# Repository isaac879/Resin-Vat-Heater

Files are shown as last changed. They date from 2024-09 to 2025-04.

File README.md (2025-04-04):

# Resin-Vat-Heater
This project is a vat heater for resin 3D printers. It is designed to keep the resin warm at an optimal temperature to ensure consistent and high quality prints.

The code is developed for a custom control board based on an ESP32-C3 and an E-Ink (E-Paper, GDEH0154D67) display module.

Important:
The E-Ink display lines “RES” and “CS” are mislabelled on the control board and to have the wires swapped. This has already been implemented in the code (See: resin_vat_heater_control_board.ino Line 33/Pin declarations). This prevents the “RES” line from pulling GPIO2 low causing issues uploading the code.

Make sure the element resistance is correct in the code and matches the resistance of your heating elements (Line 90: ELEMENT_RESISTANCE). 

Project video: https://youtu.be/hyjGFaW69lo

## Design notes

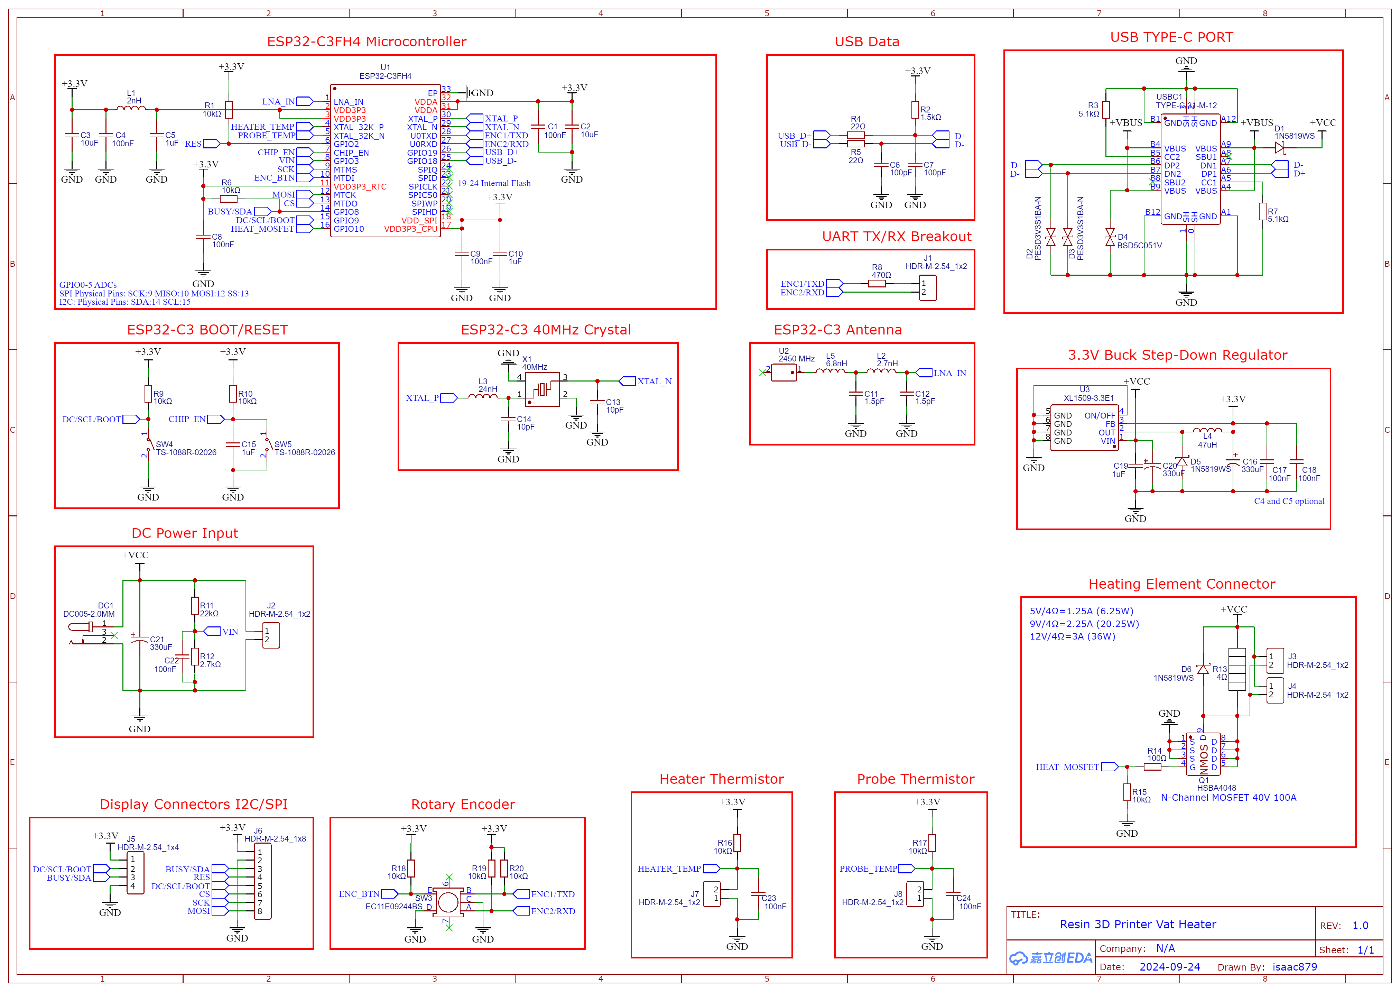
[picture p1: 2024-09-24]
Schematic-PCB/Control Board/Schematic_Resin-Vat-Hater_2024-09-24.png

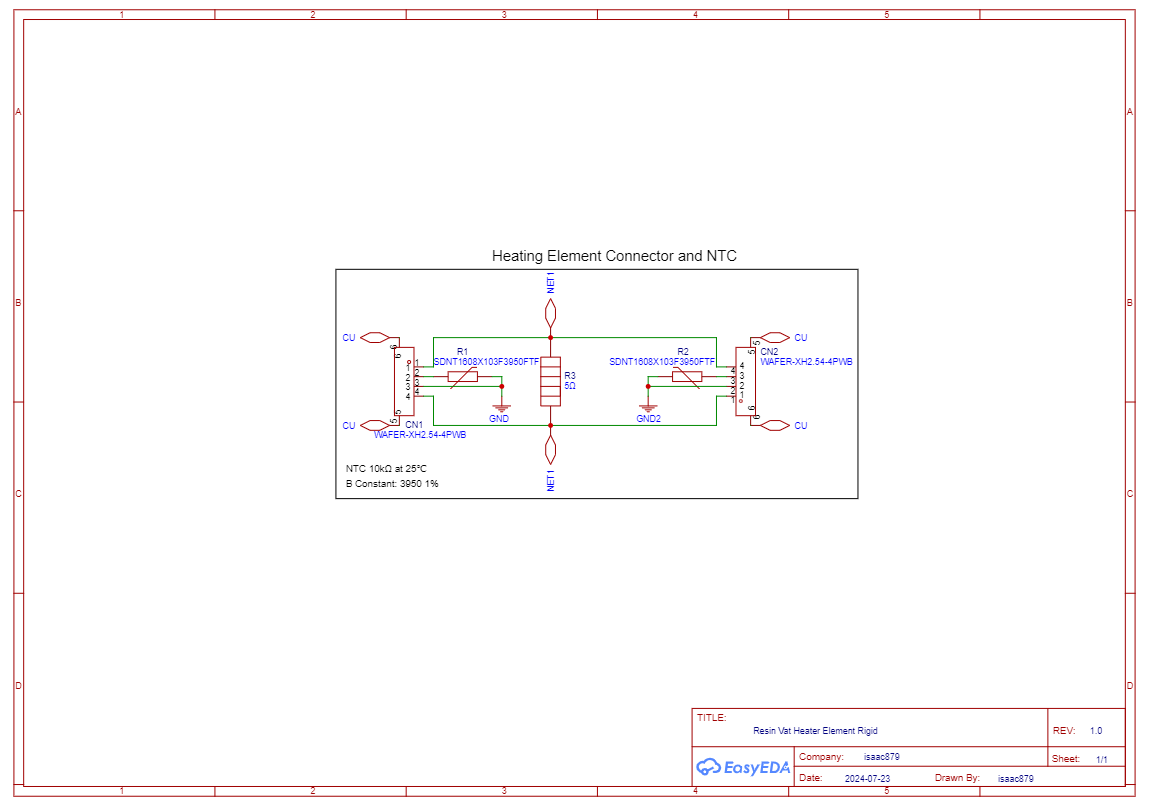
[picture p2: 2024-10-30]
Schematic-PCB/Heating Element/SCH_Resin Vat Heater Element_1-Resin Vat Heater Element_2024-10-30.png

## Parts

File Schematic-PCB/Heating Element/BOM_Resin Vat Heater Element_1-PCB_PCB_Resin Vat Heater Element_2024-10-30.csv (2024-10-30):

No. | Quantity | Comment | Designator | Footprint | Value | Manufacturer Part | Manufacturer | Supplier Part | Supplier
1 | 2 | WAFER-XH2.54-4PWB | CN1,CN2 | CONN-TH_4P-P0.20_XUNPU_WAFER-XH2.54-4PWB |  | WAFER-XH2.54-4PWB | XUNPU(讯普) | C3029478 | LCSC
2 | 2 | SDNT1608X103F3950FTF | R1,R2 | R0603 |  | SDNT1608X103F3950FTF | Sunlord(顺络) | C279936 | LCSC

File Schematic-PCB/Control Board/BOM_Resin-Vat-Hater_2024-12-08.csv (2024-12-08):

ID | Name | Designator | Footprint | Quantity | Manufacturer Part | Manufacturer | Supplier | Supplier Part | Price
1 | TYPE-C-31-M-12 | USBC1 | USB-C_SMD-TYPE-C-31-M-12MOD | 1 | TYPE-C-31-M-12 | Rectangular Connectors - Contacts | LCSC | C165948 | 0.155
2 | 1uF | C19 | C0805MOD | 1 | CL21B105KBFNNNE | SAMSUNG(三星) | LCSC | C28323 | 0.008
3 | 100nF | C1,C4,C17,C18 | C0603 | 4 | CC0603KRX7R9BB104 | YAGEO | LCSC | C14663 | 0.002
4 | 330uF | C20,C21 | CAP-SMD_BD10.0-L10.3-W10.3-LS11.3-FD | 2 | RVE1V331M1010 | HONOR(荣誉) | LCSC | C88682 | 0.114
5 | 40MHz | X1 | CRYSTAL-SMD_4P-L3.2-W2.5-BL_SIT8008BI | 1 | CF4040M00015001 | HUAXIN(华昕) | LCSC | C7294600 | 0.052
6 | 6.8nH | L5 | L0603 | 1 | SDCL1608C6N8JTDF | Sunlord(顺络) | LCSC | C49447 | 0.008
7 | 10kΩ | R1,R6,R9,R10,R15,R16,R17 | R0603 | 7 | 0603WAF1002T5E | UNI-ROYAL(厚声) | LCSC | C25804 | 0.001
8 | TS-1088R-02026 | SW4,SW5 | SW-SMD_L3.9-W3.0-P4.45 | 2 | TS-1088R-02026 | XUNPU(讯普) | LCSC | C455280 | 0.044
9 | 10uF | C2,C3 | C0603 | 2 | CL10A106KP8NNNC | SAMSUNG(三星) | LCSC | C19702 | 0.005
10 | 1uF | C5,C10,C15 | C0603 | 3 | CL10A105KB8NNNC | SAMSUNG(三星) | LCSC | C15849 | 0.004
11 | 100nF | C8,C9,C22,C23,C24 | C0603 | 5 | CC0603KRX7R9BB104 | YAGEO(国巨) | LCSC | C14663 | 0.002
12 | 1.5pF | C11,C12 | C0603 | 2 | 0603CG1R5C500NT | FH(风华) | LCSC | C1639 | 0.003
13 | 10pF | C13,C14 | C0603 | 2 | CL10C100JB8NNNC | SAMSUNG(三星) | LCSC | C1634 | 0.003
14 | 330uF | C16 | CAP-SMD_BD6.3-L6.6-W6.6-FD | 1 | RVT1A331M0607 | HONOR | LCSC | C58277 | 0.034
15 | 1N5819WS | D1,D5,D6 | SOD-323_L1.8-W1.3-LS2.5-RD | 3 | 1N5819WS | Hottech(合科泰) | LCSC | C191023 | 0.008
16 | PESD3V3S1BA-N | D2,D3 | SOD-523_L1.2-W0.8-LS1.6-BI | 2 | PESD3V3S1BA-N | Bourne Semicon (Shenzhen) | LCSC | C316037 | 0.03
17 | BSD5C051V | D4 | SOD-523_L1.2-W0.8-LS1.6-BI | 1 | BSD5C051V | BORN | LCSC | C151981 | 0.026
18 | DC005-2.0MM | DC1 | DC-IN-TH_DC005 | 1 | DC005-2.0MM | SOFNG | LCSC | C111567 | 0.138
19 | 2nH | L1 | L0603 | 1 | SDCL1608C2N0STDF | Sunlord(顺络) | LCSC | C370234 | 0.008
20 | 2.7nH | L2 | L0603 | 1 | SDCL1608C2N7STDF | Sunlord(顺络) | LCSC | C13817 | 0.008
21 | 24nH | L3 | L0603 | 1 | SDCL1608C24NJTDF | Sunlord(顺络) | LCSC | C74305 | 0.007
22 | 47uH | L4 | IND-SMD_L5.0-W5.0 | 1 | CKCS5020-47uH/M | CENKER | LCSC | C354600 | 0.061
23 | HSBA4048 | Q1 | POWERPAK-SO-8_L6.2-W5.2-P1.27-BL-EP | 1 | HSBA4048 | HUASHUO(华朔) | LCSC | C508827 | 0.63
24 | 1.5kΩ | R2 | R0603 | 1 | 0603WAF1501T5E | UNI-ROYAL(厚声) | LCSC | C22843 | 0.001
25 | 22Ω | R4,R5 | R0603 | 2 | 0603WAF220JT5E | UNI-ROYAL(厚声) | LCSC | C23345 | 0.001
26 | 470Ω | R8 | R0603 | 1 | 0603WAF4700T5E | UNI-ROYAL(厚声) | LCSC | C23179 | 0.001
27 | 22kΩ | R11 | R0603 | 1 | 0603WAF2202T5E | UNI-ROYAL(厚声) | LCSC | C31850 | 0.001
28 | 2.7kΩ | R12 | R0603 | 1 | 0603WAF2701T5E | UNI-ROYAL(厚声) | LCSC | C13167 | 0.001
29 | 100Ω | R14 | R0603 | 1 | 0603WAF1000T5E | UNI-ROYAL(厚声) | LCSC | C22775 | 0.001
30 | EC11E09244BS | SW3 | SW-TH_EC11XXXXXXXX | 1 | EC11E09244BS | ALPSALPINE(阿尔卑斯阿尔派) | LCSC | C470742 | 1.661
31 | ESP32-C3FH4 | U1 | QFN-32_L5.0-W5.0-P0.50-TL-EP3.7 | 1 | ESP32-C3FH4 | ESPRESSIF(乐鑫) | LCSC | C2858491 | 2.308
32 | 2450 MHz | U2 | FILTER-SMD_1206-2P-L3.2-W1.6-L | 1 | RFANT3216120A5T | Walsin(华新科) | LCSC | C127629 | 0.079
33 | XL1509-3.3E1 | U3 | SOP-8_L4.9-W3.9-P1.27-LS6.0-BL | 1 | XL1509-3.3E1 | XLSEMI | LCSC | C74193 | 0.24
34 | 5.1kΩ | R3,R7 | R0603 | 2 | 0603WAF5101T5E | UNI-ROYAL(厚声) | LCSC | C23186 | 0.001

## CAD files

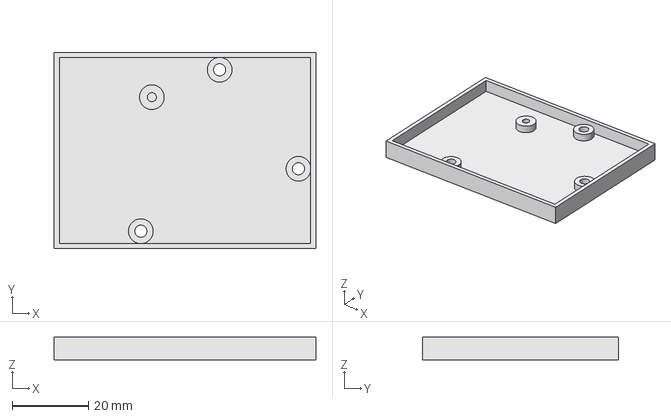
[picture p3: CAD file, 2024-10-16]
CAD FIles/STEP/PCB Case Bottom.step
68.8 x 51.6 x 6.00 mm

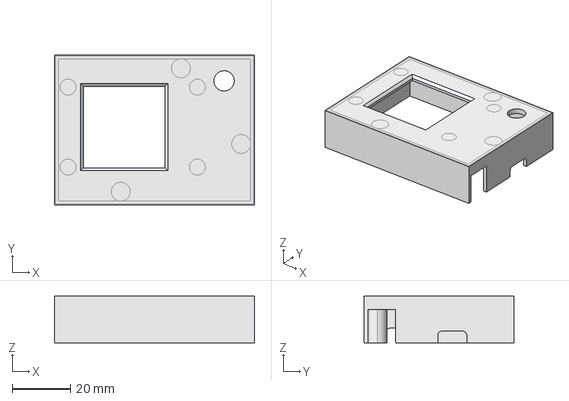
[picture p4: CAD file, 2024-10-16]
CAD FIles/STEP/PCB Case Top.step
68.8 x 51.6 x 16.0 mm

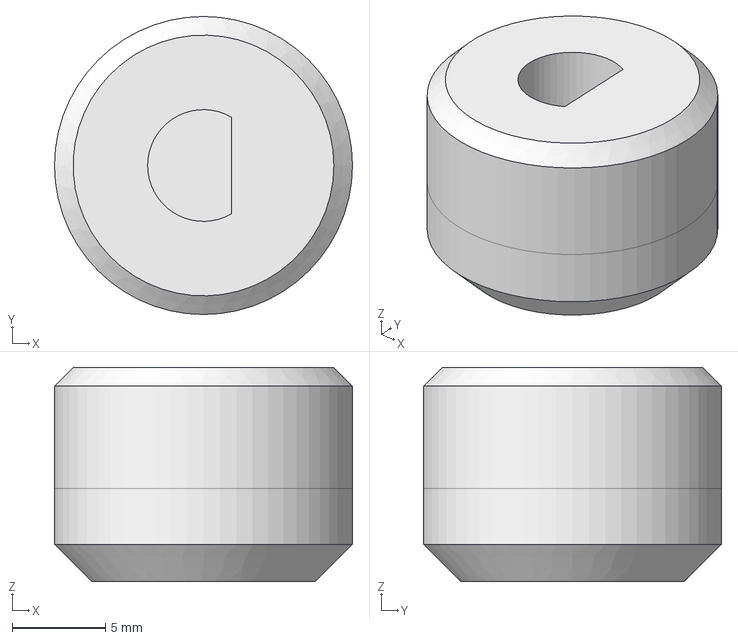
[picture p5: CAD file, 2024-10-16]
CAD FIles/STEP/Encoder knob.step
16.0 x 16.0 x 11.5 mm

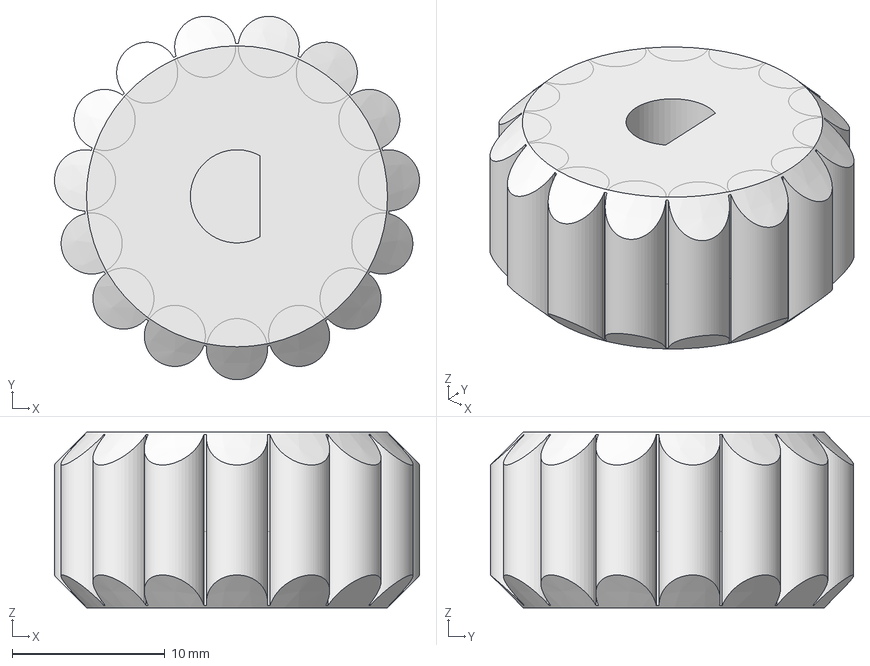
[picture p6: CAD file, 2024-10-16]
CAD FIles/STEP/Encoder knob 2.step
23.9 x 23.8 x 11.5 mm

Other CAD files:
CAD FIles/STLs/Encoder knob 2.stl
CAD FIles/STLs/Encoder knob.stl
CAD FIles/STLs/PCB Case Bottom.stl
CAD FIles/STLs/PCB Case Top.stl

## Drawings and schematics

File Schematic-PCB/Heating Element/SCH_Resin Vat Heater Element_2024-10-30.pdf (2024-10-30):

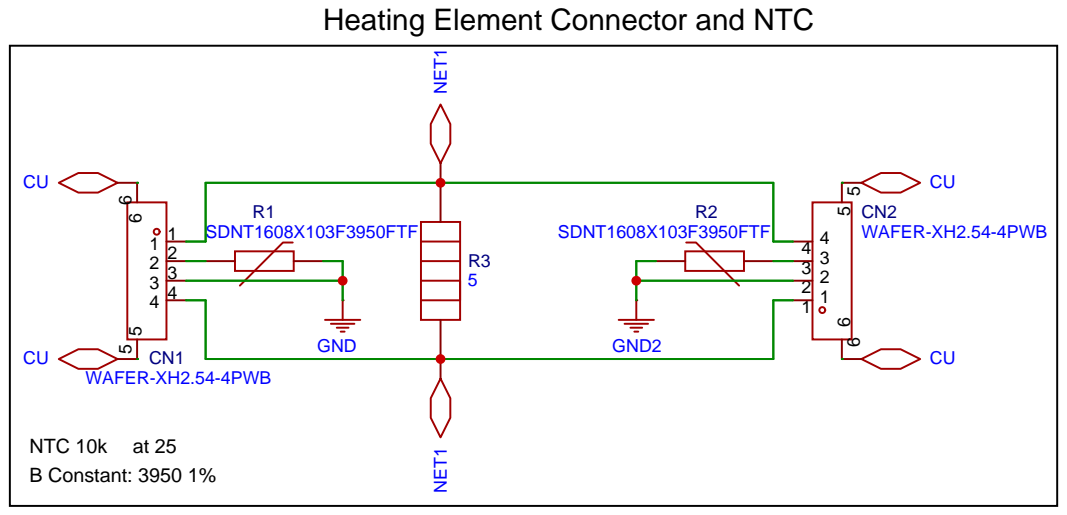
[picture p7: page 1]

Heating Element Connector and NTC

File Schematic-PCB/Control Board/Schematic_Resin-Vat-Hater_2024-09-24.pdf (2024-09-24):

## USB TYPE-C PORT ESP32-C3FH4 Microcontroller

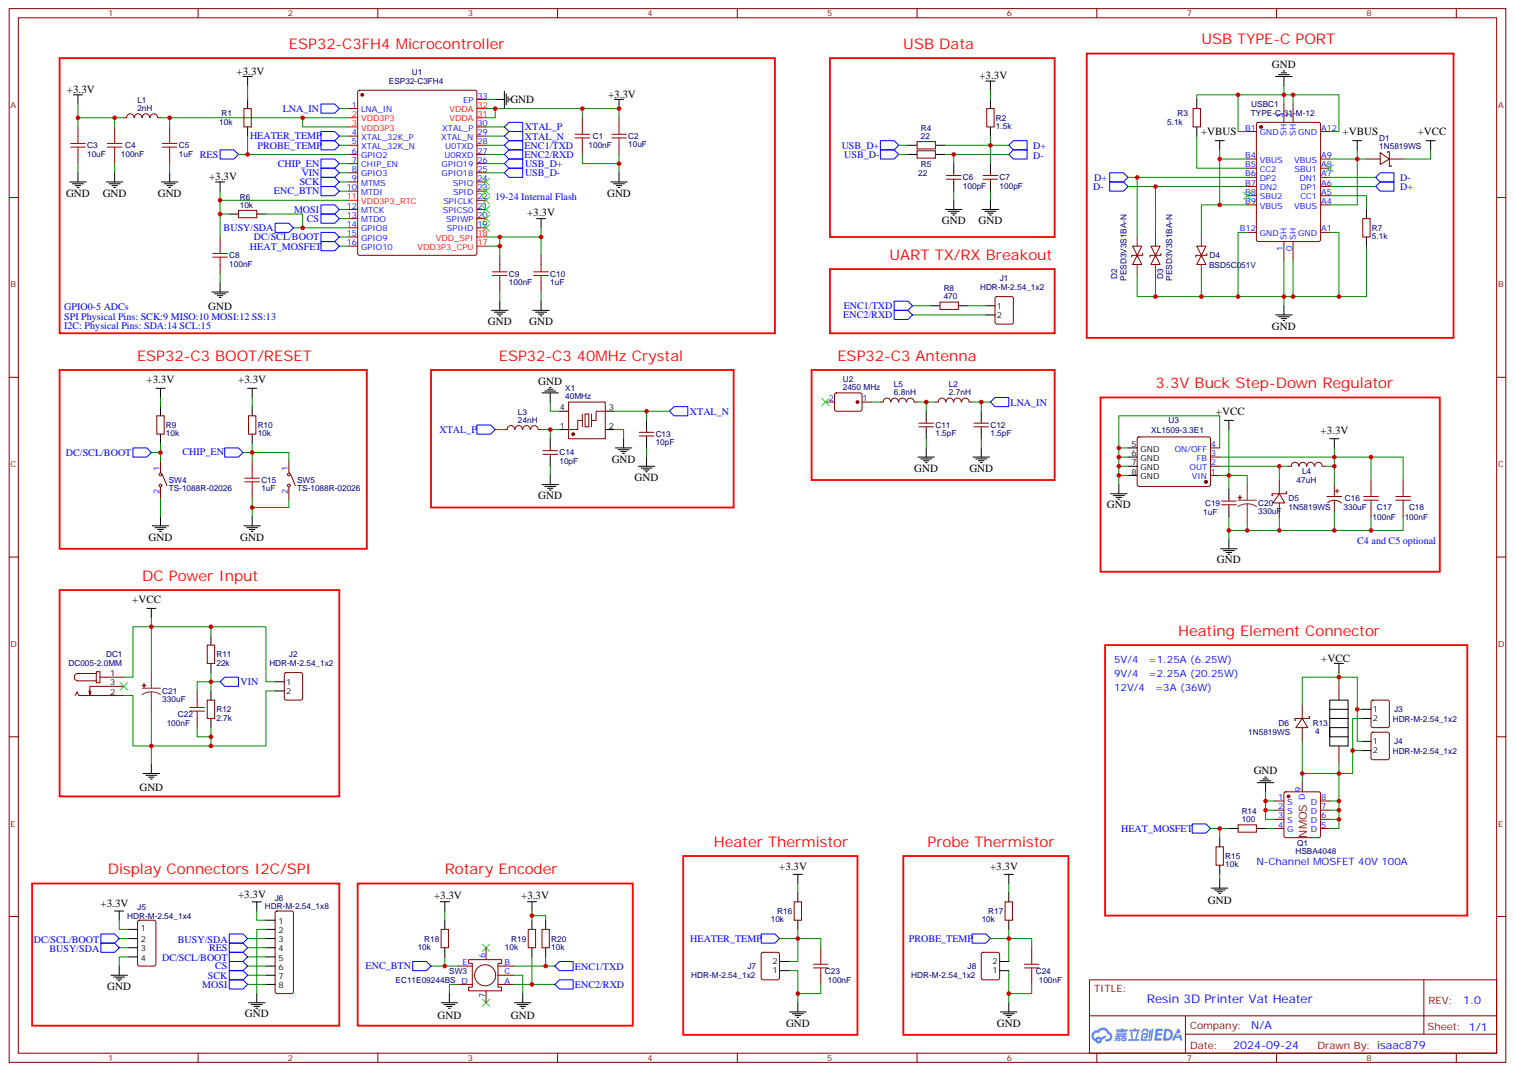
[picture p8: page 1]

GND
UART TX/RX Breakout

GPIO0-5 ADCs
SPI Physical Pins: SCK:9 MISO:10 MOSI:12 SS:13
I2C: Physical Pins: SDA:14 SCL:15

3.3V Buck Step-Down Regulator

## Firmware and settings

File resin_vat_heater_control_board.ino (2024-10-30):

/*--------------------------------------------------------------------------------------------------------------------------------------------------------
 * The code is developed for a resin vat heater control board based on an ESP32-C3 (PCB Version: V1.0) 
 * 
 * All measurements are in SI units unless otherwise specified.
 * 
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
 * Code written by isaac879
 * 
 * Compiled in the Arduino IDE 2.3.2
 *  
 * Last modified: 16/10/2024
 *
 * Copyright(C) Isaac Chaseau (isaac879)
 *
 *--------------------------------------------------------------------------------------------------------------------------------------------------------*/

//Libraries
#define ENABLE_GxEPD2_GFX 0

#include <GxEPD2_BW.h>
#include <GxEPD2_3C.h>
#include <Fonts/FreeMonoBold9pt7b.h>
#include <Fonts/FreeMonoBold12pt7b.h>
#include <Fonts/FreeMonoBold18pt7b.h>
#include <Fonts/FreeMono18pt7b.h>

/*--------------------------------------------------------------------------------------------------------------------------------------------------------*/

//Pin declarations
#define PIN_THERMISTOR_HEATER 1//HEATER_TEMP
#define PIN_THERMISTOR_PROBE 0//PROBE_TEMP
#define PIN_INPUT_VOLTAGE 3//VIN

// #define PIN_OLED_SDA 8
// #define PIN_OLED_SCL 9

#define PIN_ENC_BTN 5
#define PIN_ENC1 21//ENC1/TXD
#define PIN_ENC2 20//ENC2/RXD

#define PIN_RES 7 //Swapped with GPIO2
#define PIN_SCK 4
#define PIN_MOSI 6
#define PIN_CS 2 //Swapped with GPIO7
#define PIN_BUSY 8//BUSY/SDA
#define PIN_DC 9//DC/SCL/BOOT

#define PIN_HEAT_MOSFET 10

#define PIN_SERIAL_RX 19
#define PIN_SERIAL_TX 18

/*--------------------------------------------------------------------------------------------------------------------------------------------------------*/

//Constants
#define BAUD_RATE 115200

#define LEDC_CHANNEL 1
#define LEDC_FREQUENCY 25000
#define LEDC_BIT_RESOLUTION 8
#define LEDC_MAX_DUTY (pow(2, LEDC_BIT_RESOLUTION) - 1)

#define SPI_FREQUENCY 4000000 //4MHz
#define BUFFER_SIZE 10
#define ADC_SAMPLES 5

#define VIN_R1 2900.0 //2.7kOhm resistor (Measured at 2.9kOhm)
#define VIN_R2 22000.0 //22kOhm

#define RESISTOR_HEATER 10000.0 //10kOhm
#define RESISTOR_PROBE 10000.0 //10kOhm

#define TEMPERATURE_NOMINAL_PLATE 25.0 
#define THERMISTOR_NOMINAL_PLATE 10000 //10k
#define THERMISTOR_B_COEFFICIENT_PLATE 3950

#define TEMPERATURE_NOMINAL_PROBE 25.0
#define THERMISTOR_NOMINAL_PROBE 10000 //10k
#define THERMISTOR_B_COEFFICIENT_PROBE 3950

#define ADC_THERMISTOR_CONNECTED_THRESHOLD (MAX_ADC_VALUE - 1) //If NTC thermistor is not connected the ADC should be pulled up by the resistor giving a value of 1023 (1022 ued to account for noise).

#define DEFAULT_TARGET_TEMPERATURE_ELEMENT 35.0
#define MAX_POWER_LIMIT 15.0 //Watts //5 for testing 30 for using.
// #define ELEMENT_RESISTANCE 2.5 //Measured the value in Ohms
#define ELEMENT_RESISTANCE 1.3 //Measured the value in Ohms (2 elements in parallel)
#define MAX_ELEMENT_TEMPERATURE 60.0
#define MAX_CURRENT 2.0 //2A

#define INPUT_VOLTAGE_MIN 7
#define INPUT_VOLTAGE_MAX 30

// #define SCREEN_WIDTH 128 // OLED display width, in pixels
// #define SCREEN_HEIGHT 64 // OLED display height, in pixels
// #define OLED_RESET -1  

#define MAX_ADC_VALUE 4095.0 //ESP32-C3 has 12bit ADCs

#define MAX_MINUTE_TIMEOUT (24 * 60) //Max of a 1 day timeout

#define MENU_TARGET_ELEMENT_TEMPERATURE 0
#define MENU_TIMEOUT 1

#define DEBOUNCE_DELAY 1 //Debounce delay in ms (Bounce measured as ~20us)

#define DISPLAY_ROTATION 1

#define LOGO_WIDTH 100 //logo width in px
#define LOGO_HEIGHT 100 //logo height in px

#define TEXT_HEIGHT 24
#define LINE_SPACE (TEXT_HEIGHT + 10) + (TEXT_HEIGHT + 8) //Line spacing for the display
#define EINK_LINE_0 (0 * LINE_SPACE)
#define EINK_LINE_1 (1 * LINE_SPACE)
#define EINK_LINE_2 (2 * LINE_SPACE)
#define EINK_LINE_3 (3 * LINE_SPACE)
#define EINK_LINE_4 (4 * LINE_SPACE)
#define EINK_LINE_5 (5 * LINE_SPACE)
#define EINK_LINE_6 (6 * LINE_SPACE)
#define EINK_LINE_7 (7 * LINE_SPACE)
#define EINK_LINE_8 (8 * LINE_SPACE)
#define EINK_LINE_9 (9 * LINE_SPACE)

//Menu value determines priority (Errors should be highest)
#define MENU_SCREEN_START 0
#define MENU_SCREEN_SPLASH 1
#define MENU_SCREEN_STATUS 2
#define MENU_SCREEN_TIMEOUT 3
#define MENU_SCREEN_ERROR 4
#define MENU_SCREEN_POWER_ERROR 5
#define MENU_SCREEN_OVERTEMPERATURE_ERROR 6
#define MENU_SCREEN_THERMISTOR_0_ERROR 7
#define MENU_SCREEN_THERMISTOR_1_ERROR 8
#define MENU_SCREEN_REATCHING_TEMPERATURE_ERROR 9

/*--------------------------------------------------------------------------------------------------------------------------------------------------------*/

//Global scope variables
volatile uint16_t element_temp_buffer[BUFFER_SIZE];
volatile uint16_t probe_temp_buffer[BUFFER_SIZE];
volatile uint16_t voltage_buffer[BUFFER_SIZE];

volatile uint16_t adc_thermistor_element = 0;
volatile uint16_t adc_thermistor_probe = 0;
volatile uint16_t adc_voltage = 0;

volatile double resistance_thermistor_element = 0;
volatile double resistance_thermistor_probe = 0;

volatile double temp_steinhart_thermistor_element = 0;
volatile double temp_steinhart_thermistor_probe = 0;

volatile double temp_target_element = 35.0;
volatile double temp_target_probe = 0.0;

volatile double maximum_power_limit = MAX_POWER_LIMIT; //Max power in Watts
volatile double maximum_current_limit = MAX_CURRENT; //Max power in amps

volatile double input_voltage = 0;
volatile double minute_timeout = 60 * 8; //Time in minutes before the heating element is turned off.

volatile int16_t encoderValue = 0;  //Variable to store encoder value
volatile bool encoderDir = true; //Variable to store direction (true: clockwise, false: counterclockwise)
volatile int16_t encoder_button_count = 0;
volatile int16_t menu_item_selection = MENU_TIMEOUT;

volatile uint32_t ms_last_debounce_time_encoder = 0;
volatile uint32_t ms_last_debounce_time_button = 0;

const char splash_screen_text_0[] = "Vat Heater";
const char splash_screen_text_2[] = "isaac879";
const char splash_screen_text_1[] = "Ver: 1.0.1";

volatile int64_t msTimeoutStart = 0;
volatile int64_t msTimeoutEnd = 0;

bool full_screen_update = false;
volatile bool require_screen_update = true;

double last_displayed_thermistor0 = 0;
double last_displayed_thermistor1 = 0;
double last_displayed_target_temp = 0;
int16_t last_displayed_timer = 0;
int16_t last_displayed_screen = 0;

volatile int16_t display_screen = MENU_SCREEN_SPLASH;
const uint8_t drops_symbol_100x100[] = {
   0x00, 0x00, 0x00, 0x00, 0x00, 0xf8, 0xff, 0x01, 0x00, 0x00, 0x00, 0x00,
   0x00, 0x00, 0x00, 0x00, 0x00, 0xc0, 0xff, 0xff, 0x3f, 0x00, 0x00, 0x00,
   0x00, 0x00, 0x00, 0x00, 0x00, 0x00, 0xfc, 0x00, 0x00, 0xf0, 0x03, 0x00,
   0x00, 0x00, 0x00, 0x00, 0x00, 0x00, 0x80, 0x0f, 0x00, 0x00, 0x00, 0x1f,
   0x00, 0x00, 0x00, 0x00, 0x00, 0x00, 0x00, 0xe0, 0x01, 0x00, 0x00, 0x00,
   0x78, 0x00, 0x00, 0x00, 0x00, 0x00, 0x00, 0x00, 0x78, 0x00, 0x00, 0x00,
   0x00, 0xe0, 0x01, 0x00, 0x00, 0x00, 0x00, 0x00, 0x00, 0x1e, 0x00, 0x00,
   0x00, 0x00, 0x80, 0x07, 0x00, 0x00, 0x00, 0x00, 0x00, 0x00, 0x07, 0x00,
   0x00, 0x00, 0x00, 0x00, 0x0e, 0x00, 0x00, 0x00, 0x00, 0x00, 0xc0, 0x01,
   0x00, 0x00, 0x00, 0x00, 0x00, 0x38, 0x00, 0x00, 0x00, 0x00, 0x00, 0x60,
   0x00, 0x00, 0x00, 0x00, 0x00, 0x00, 0x60, 0x00, 0x00, 0x00, 0x00, 0x00,
   0x38, 0x00, 0x00, 0x00, 0x00, 0x00, 0x00, 0xc0, 0x01, 0x00, 0x00, 0x00,
   0x00, 0x1c, 0x00, 0x00, 0x00, 0x00, 0x00, 0x00, 0x80, 0x03, 0x00, 0x00,
   0x00, 0x00, 0x06, 0x00, 0x00, 0x00, 0x00, 0x00, 0x00, 0x00, 0x06, 0x00,
   0x00, 0x00, 0x00, 0x03, 0x00, 0x00, 0x00, 0x00, 0x00, 0x00, 0x00, 0x0c,
   0x00, 0x00, 0x00, 0x80, 0x01, 0x00, 0x00, 0x00, 0x00, 0x00, 0x00, 0x00,
   0x18, 0x00, 0x00, 0x00, 0xc0, 0x00, 0x00, 0xc0, 0x00, 0x00, 0x00, 0x00,
   0x00, 0x30, 0x00, 0x00, 0x00, 0x60, 0x00, 0x00, 0xc0, 0x00, 0x00, 0x00,
   0x00, 0x00, 0x60, 0x00, 0x00, 0x00, 0x30, 0x00, 0x00, 0xc0, 0x00, 0x00,
   0x00, 0x00, 0x00, 0xc0, 0x00, 0x00, 0x00, 0x18, 0x00, 0x00, 0xc0, 0x00,
   0x00, 0x00, 0x00, 0x00, 0x80, 0x01, 0x00, 0x00, 0x0c, 0x00, 0x00, 0xc0,
   0x00, 0x00, 0x00, 0x00, 0x00, 0x00, 0x03, 0x00, 0x00, 0x0c, 0x00, 0x00,
   0xe0, 0x01, 0x00, 0x00, 0x00, 0x00, 0x00, 0x03, 0x00, 0x00, 0x06, 0x00,
   0x00, 0xe0, 0x01, 0x00, 0x00, 0x00, 0x00, 0x00, 0x06, 0x00, 0x00, 0x03,
   0x00, 0x00, 0xf0, 0x03, 0x00, 0x00, 0x00, 0x00, 0x00, 0x0c, 0x00, 0x00,
   0x01, 0x00, 0x00, 0xf0, 0x03, 0x00, 0x00, 0x00, 0x00, 0x00, 0x08, 0x00,
   0x80, 0x01, 0x00, 0x00, 0xf8, 0x07, 0x00, 0x00, 0x00, 0x00, 0x00, 0x18,
   0x00, 0xc0, 0x00, 0x00, 0x00, 0xfc, 0x0f, 0x00, 0x00, 0x00, 0x00, 0x00,
   0x30, 0x00, 0xc0, 0x00, 0x00, 0x00, 0xfe, 0x0f, 0x00, 0x00, 0x00, 0x00,
   0x00, 0x30, 0x00, 0x60, 0x00, 0x00, 0x00, 0xfe, 0x1f, 0x00, 0x00, 0x00,
   0x00, 0x00, 0x60, 0x00, 0x60, 0x00, 0x00, 0x00, 0xff, 0x3f, 0x00, 0x00,
   0x06, 0x00, 0x00, 0x60, 0x00, 0x30, 0x00, 0x00, 0x80, 0xff, 0x7f, 0x00,
   0x00, 0x06, 0x00, 0x00, 0xc0, 0x00, 0x30, 0x00, 0x00, 0x80, 0xff, 0x7f,
   0x00, 0x00, 0x06, 0x00, 0x00, 0xc0, 0x00, 0x18, 0x00, 0x00, 0xc0, 0xff,
   0xff, 0x00, 0x00, 0x06, 0x00, 0x00, 0x80, 0x01, 0x18, 0x00, 0x00, 0xc0,
   0xff, 0xff, 0x00, 0x00, 0x06, 0x00, 0x00, 0x80, 0x01, 0x08, 0x00, 0x00,
   0xe0, 0xff, 0xff, 0x01, 0x00, 0x0f, 0x00, 0x00, 0x00, 0x01, 0x0c, 0x00,
   0x00, 0xe0, 0xff, 0xff, 0x01, 0x00, 0x0f, 0x00, 0x00, 0x00, 0x03, 0x0c,
   0x00, 0x00, 0xe0, 0xff, 0xff, 0x01, 0x80, 0x1f, 0x00, 0x00, 0x00, 0x03,
   0x04, 0x00, 0x00, 0xe0, 0xff, 0xff, 0x01, 0x80, 0x1f, 0x00, 0x00, 0x00,
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
};

hw_timer_t *timer_control_loop_ISR = NULL;

//1.54'' EPD Module
GxEPD2_BW<GxEPD2_154_D67, GxEPD2_154_D67::HEIGHT> display(GxEPD2_154_D67(PIN_CS, PIN_DC, PIN_RES, PIN_BUSY)); //GDEH0154D67 200x200, SSD1681

/*--------------------------------------------------------------------------------------------------------------------------------------------------------*/

double mapNumber(double x, double in_min, double in_max, double out_min, double out_max){//Remaps a number to a given range
    return (x - in_min) * (out_max - out_min) / (in_max - in_min) + out_min;
}

/*--------------------------------------------------------------------------------------------------------------------------------------------------------*/

void IRAM_ATTR readEncoder(void){ //Interrupt service routine (ISR) for the encoder
    uint32_t currentTime = millis(); 

    if(currentTime - ms_last_debounce_time_encoder > DEBOUNCE_DELAY){
        delayMicroseconds(20); //Need to wait for signals to settle. Measured to take <20us
        bool pinA = digitalRead(PIN_ENC1); //Read both encoder pins
        bool pinB = digitalRead(PIN_ENC2);
        
        if(pinA == pinB){ //Determine direction based on the states of the pins
            encoderValue++;
        }
        else{
            encoderValue--;
        }
        ms_last_debounce_time_encoder = currentTime;  //Update the last debounce time
    }
}

/*--------------------------------------------------------------------------------------------------------------------------------------------------------*/

void IRAM_ATTR readEncoderButton(void){ //Interrupt service routine (ISR) for the encoder
    uint32_t currentTime = millis(); 

    if(currentTime - ms_last_debounce_time_button > DEBOUNCE_DELAY){
        encoder_button_count++; //Increment the count

        if(encoder_button_count > 2){ //Wrap around the count
            encoder_button_count = 1;
        }

        if(encoder_button_count == 1){
            menu_item_selection = MENU_TARGET_ELEMENT_TEMPERATURE;
        }
        else{
            menu_item_selection = MENU_TIMEOUT;
        }
        ms_last_debounce_time_button = currentTime; //Update the last debounce time
    }
}

/*--------------------------------------------------------------------------------------------------------------------------------------------------------*/

void readADCs(void){ //Read x samples and average then store in a circular buffer
    static uint8_t index = 0;

    uint16_t adcPlate = 0;
    uint16_t adcProbe = 0;
    uint16_t adcVin = 0;

    for(uint8_t i = 0; i < ADC_SAMPLES; i++){
        adcPlate += analogRead(PIN_THERMISTOR_HEATER);
        adcProbe += analogRead(PIN_THERMISTOR_PROBE);
        adcVin += analogRead(PIN_INPUT_VOLTAGE);
    }

    element_temp_buffer[index] = adcPlate / ADC_SAMPLES;
    probe_temp_buffer[index] = adcProbe / ADC_SAMPLES;
    voltage_buffer[index] = adcVin / ADC_SAMPLES;

    index = (index + 1) % BUFFER_SIZE;

    uint16_t adcAvgPlate = 0;
    uint16_t adcAvgProbe = 0;
    uint16_t adcAvgVin = 0;

    for(uint8_t i = 0; i < BUFFER_SIZE; i++){
        adcAvgPlate += element_temp_buffer[i];
        adcAvgProbe += probe_temp_buffer[i];
        adcAvgVin += voltage_buffer[i];
    }

    adc_thermistor_element = adcAvgPlate / BUFFER_SIZE;
    adc_thermistor_probe = adcAvgProbe / BUFFER_SIZE;
    adc_voltage = adcAvgVin / BUFFER_SIZE;

    input_voltage = (3.3 * ((double)adc_voltage / MAX_ADC_VALUE)) * ((VIN_R1 + VIN_R2) / VIN_R1);

    if((input_voltage / ELEMENT_RESISTANCE) > MAX_CURRENT){ //Make sure the max current limit cannot be exceeded
        maximum_power_limit = MAX_CURRENT * input_voltage;
    }
}

/*--------------------------------------------------------------------------------------------------------------------------------------------------------*/

double adcToResistance(uint32_t adc, uint32_t resistorVal){
    return (resistorVal * (double)adc)/ (MAX_ADC_VALUE - constrain(adc, 0.0, MAX_ADC_VALUE - 1.0)); //Constrain to avoid dividing by zero
}

/*--------------------------------------------------------------------------------------------------------------------------------------------------------*/

double resistanceToTemperatureSteinheart(double res, double thermistorNominal, double thermistorBCoefficient, double temperatureNominal){
    double steinhart = log(res / thermistorNominal); // ln(R/Ro)
    steinhart /= thermistorBCoefficient; // 1/B * ln(R/Ro)
    steinhart += 1.0 / (temperatureNominal + 273.15); // + (1/To)
    steinhart = 1.0 / steinhart; //Invert
    return steinhart - 273.15; //Kelvin to C
}

/*--------------------------------------------------------------------------------------------------------------------------------------------------------*/

void termistorCalcs(void){
    resistance_thermistor_element = adcToResistance(adc_thermistor_element, RESISTOR_HEATER);
    resistance_thermistor_probe = adcToResistance(adc_thermistor_probe, RESISTOR_PROBE);

    temp_steinhart_thermistor_element = (elementThermistorConnected() == true) ? resistanceToTemperatureSteinheart(resistance_thermistor_element, THERMISTOR_NOMINAL_PLATE, THERMISTOR_B_COEFFICIENT_PLATE, TEMPERATURE_NOMINAL_PLATE) : -273.15;
    temp_steinhart_thermistor_probe = (probeThermistorConnected() == true) ? resistanceToTemperatureSteinheart(resistance_thermistor_probe, THERMISTOR_NOMINAL_PROBE, THERMISTOR_B_COEFFICIENT_PROBE, TEMPERATURE_NOMINAL_PROBE) : -273.15;
}

/*--------------------------------------------------------------------------------------------------------------------------------------------------------*/

double getVoltageIn(void){
    return input_voltage;
}

/*--------------------------------------------------------------------------------------------------------------------------------------------------------*/

double getCurrent(void){
    if(getMaximumAchievablePower() > getPowerLimit()){
        return maximum_power_limit / getVoltageIn();
    }
    else{
        return getVoltageIn() / ELEMENT_RESISTANCE;
    }
}

/*--------------------------------------------------------------------------------------------------------------------------------------------------------*/

double getPowerLimit(void){
    return (maximum_power_limit > MAX_POWER_LIMIT) ? MAX_POWER_LIMIT : maximum_power_limit;
}

/*--------------------------------------------------------------------------------------------------------------------------------------------------------*/

double getMaximumAchievablePower(void){
    return (input_voltage * input_voltage) / ELEMENT_RESISTANCE;
}

/*--------------------------------------------------------------------------------------------------------------------------------------------------------*/

double getPowerUsed(void){
    if(getMaximumAchievablePower() > getPowerLimit()){
        return getPowerLimit();
    }
    else{
        return getMaximumAchievablePower();
    }
}

/*--------------------------------------------------------------------------------------------------------------------------------------------------------*/

double getTargetTemperature(void){
    static int16_t lastEncoderValue = 0;
    int16_t encoderDelta = encoderValue - lastEncoderValue;
    if((menu_item_selection == MENU_TARGET_ELEMENT_TEMPERATURE) && (encoderDelta != 0)){
        temp_target_element += mapNumber(encoderDelta, -1, 1, -0.5, 0.5);
        temp_target_element = constrain(temp_target_element, 0, MAX_ELEMENT_TEMPERATURE);
    }
    lastEncoderValue = encoderValue;
    return temp_target_element;
}

/*--------------------------------------------------------------------------------------------------------------------------------------------------------*/

void updateTimeout(void){
    static int16_t lastEncoderValue = 0;
    int16_t encoderDelta = encoderValue - lastEncoderValue;

    if((menu_item_selection == MENU_TIMEOUT) && (encoderDelta != 0)){
        minute_timeout += mapNumber(encoderDelta, -1, 1, -10, 10);
        minute_timeout = constrain(minute_timeout, 0, MAX_MINUTE_TIMEOUT);
    }
    if(minute_timeout == 0){
        msTimeoutStart = millis();
    }

    msTimeoutEnd = msTimeoutStart + ((int64_t)minute_timeout * (int64_t)60000);
    lastEncoderValue = encoderValue;
}

/*--------------------------------------------------------------------------------------------------------------------------------------------------------*/

double getTimeoutMinutes(void){ //Return the minutes left until the timeout is reached
    double mTimeout = (double)(msTimeoutEnd - (int64_t)millis()) / (60000.0);
    if(mTimeout <= 0){
        mTimeout = 0;
        updateMenuScreenselector(MENU_SCREEN_TIMEOUT);
    }
    return mTimeout;
}

/*--------------------------------------------------------------------------------------------------------------------------------------------------------*/

void heatingElementOn(void){
    double maxPowerDraw = (input_voltage * input_voltage) / ELEMENT_RESISTANCE; //Max possible power given coil resistance and input voltage
    uint8_t duty = (double)LEDC_MAX_DUTY;

    if(maxPowerDraw > maximum_power_limit){
        duty = (double)LEDC_MAX_DUTY * (maximum_power_limit / maxPowerDraw); //Duty scaled proportional to the power limit
    }

     ledcWrite(LEDC_CHANNEL, duty);
}

/*--------------------------------------------------------------------------------------------------------------------------------------------------------*/

void heatingElementOff(void){
    ledcWrite(LEDC_CHANNEL, 0); //Off
}

/*--------------------------------------------------------------------------------------------------------------------------------------------------------*/

bool inputVoltageOk(void){
    if((input_voltage > INPUT_VOLTAGE_MIN) && (input_voltage < INPUT_VOLTAGE_MAX)){
        return true;
    }
    else{
        updateMenuScreenselector(MENU_SCREEN_POWER_ERROR);
        return false;
    }
}

/*--------------------------------------------------------------------------------------------------------------------------------------------------------*/

bool elementThermistorConnected(void){
    if(adc_thermistor_element < ADC_THERMISTOR_CONNECTED_THRESHOLD){
        return true;
    }
    else{
        updateMenuScreenselector(MENU_SCREEN_THERMISTOR_0_ERROR);
        return false;
    }
}

/*--------------------------------------------------------------------------------------------------------------------------------------------------------*/

bool probeThermistorConnected(void){
    if(adc_thermistor_probe < ADC_THERMISTOR_CONNECTED_THRESHOLD){
        return true;
    }
    else{
        // updateMenuScreenselector(MENU_SCREEN_THERMISTOR_1_ERROR);
        return false;
    }
}

/*--------------------------------------------------------------------------------------------------------------------------------------------------------*/

void IRAM_ATTR updateControlLoop(void){
    display_screen = MENU_SCREEN_STATUS; //Set the screen to be displayed as the lowest priority
    readADCs();
    termistorCalcs();
    updateTimeout();
    bool timeout = !(getTimeoutMinutes() > 0);
    if( (temp_steinhart_thermistor_element < getTargetTemperature()) && 
        (temp_steinhart_thermistor_element < MAX_ELEMENT_TEMPERATURE) && 
        (inputVoltageOk() == true) && 
        (timeout == false) &&
        (elementThermistorConnected() == true)){ 
        heatingElementOn();
    }
    else{
        heatingElementOff();
    }
}
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
void loop(){
    static uint32_t prevTime = 0;
    static uint32_t prevTime1 = 0;
    uint32_t msTime = millis();

    if(msTime - prevTime > 700){ //Update every 700ms. Update cycle takes ~650ms
        prevTime = msTime;
        if( (last_displayed_thermistor0 != temp_steinhart_thermistor_element) ||
            (last_displayed_thermistor1 != temp_steinhart_thermistor_probe) ||
            (last_displayed_target_temp != getTargetTemperature()) ||
            (last_displayed_timer != (int16_t)getTimeoutMinutes()) ||
            (last_displayed_screen != display_screen)){

            require_screen_update = true;
        }

        if(require_screen_update == true){ //Only update the screen if data has changed
            setDisplayBuffer(display_screen);
            showDisplayBuffer();
        }
    }

    if(msTime - prevTime1 > 250){ //Print stats
        printValues();
        prevTime1 = msTime;
    }
}

/*--------------------------------------------------------------------------------------------------------------------------------------------------------*/
